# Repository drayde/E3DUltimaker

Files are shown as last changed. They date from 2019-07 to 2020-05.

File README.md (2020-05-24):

# Firmware for Ultimaker 2 with E3D v6 Hotend and Titan Extruder

This firmware is for a Ultimaker 2 with the E3D Upgrade Kit installed, which includes a E3D v6 hotend and a Titan extruder.

The firmware is a fork of the original Ultimaker firmware:
https://github.com/Ultimaker/Ultimaker2Marlin

The original README ist included as README_orig in this repro.

Changes have been made to the source code by E3D to work with the changed setup.
The orginal E3D fork is no longer online, but should match the *e3d-latest* branch in this repro.

## Links

Old wiki page on e3d-online.com: https://wiki.e3d-online.com/E3D-v6_on_Ultimaker_2
([local copy as pdf](https://github.com/drayde/E3DUltimaker/blob/drayde/E3D-v6%20on%20Ultimaker%202%20-%20E3D-Online.pdf))

Conversion video guide by Thomas Sanladerer: https://youtu.be/aLLci32tHA4

3D printed parts on thingiverse: https://www.thingiverse.com/thing:1934309

## Firmware changes by E3D

Firmware changes as documented on https://wiki.e3d-online.com/E3D-v6_on_Ultimaker_2

Changes in the "configuration.h" file:

    // increase the maximum temperature for the E3D V6 HotEnd
    #define HEATER_0_MAXTEMP 400

    // PID values for Ultimaker2 with E3D HotEnd
    #define  DEFAULT_Kp 36.59
    #define  DEFAULT_Ki 3.65
    #define  DEFAULT_Kd 91.72

    // travel extents have reduced slightly for E3D HotEnd
    #define X_MAX_POS 215 // For E3D HotEnd
    #define Y_MAX_POS 210 // For E3D HotEnd
    #define INVERT_E0_DIR true   // for direct drive extruder v9 set to true, for geared extruder set to false

    // default steps per unit for Ultimaker2 and E3D Extruder
    #define DEFAULT_AXIS_STEPS_PER_UNIT   {80.0,80.0,200,837}   // 837 to be changed to 418.5 for if a 200 steps/mm motor is used
    #define DEFAULT_MAX_FEEDRATE          {300, 300, 40, 20}    // (mm/sec)
    #define DEFAULT_MAX_ACCELERATION      {9000,9000,100,3000}  // X, Y, Z, E maximum start speed for accelerated moves. 
                                                                // E default values are good for skeinforge 40+, for older 
                                                                // versions raise them a lot.

The Bowden retraction settings should be changed if the filament change function is to work properly after the upgrade. These settings are found in the "UltiLCD2_menu_material.h" file. Here are the variables that need to be changed and their new value:

    #define FILAMENT_REVERSAL_LENGTH      (FILAMANT_BOWDEN_LENGTH + 150)
    #define FILAMENT_REVERSAL_SPEED       75
    #define FILAMENT_INSERT_FAST_SPEED    75   // Speed during the forward length

**Note:** These changes were done on an old version of the Ultimaker 2 firmware (from 29th January 2016).

The later Ultimaker 2 firmware (after v14.09) has a temperature safety feature built in, which has been notoriously sensitive. It seems like it is overly sensitive and an E3D HotEnd doesn't conform to its expected heat up and cool down cycles. The result is a common "ERROR - STOPPED Heater error" on the display panel and a failed print. The part cooling fans can often trigger this error as the air blown to cool the print can also end up cooling the heater block due to certain print geometry. Although the silicone sock provided in the kit should reduce this, it is still a recurring issue.

If you repeatedly encounter this issue, check the position of your part cooling fan ducts. They should be as low as possible without touching the bed when the nozzle does. Also, adding a siliconw sock can greatly reduce this error. Otherwise, the following lines in the "configuration.h" file control the parameters of this "safety feature".

    #define MAX_HEATING_TEMPERATURE_INCREASE 0.1 //[E3D] original value 10
    #define MAX_HEATING_CHECK_MILLIS (90000) //[E3D] original value(30 * 1000)

If you want to disable this feature like it was back in v14.09 then you can comment out the following lines in the "temperature.cpp" file at your own risk:

    // Commented out for UM2 because too sensitive for E3D HotEnd           
    //            disable_heater();
    //            Stop(STOP_REASON_HEATER_ERROR);

## My firmware changes 

none yet :-)

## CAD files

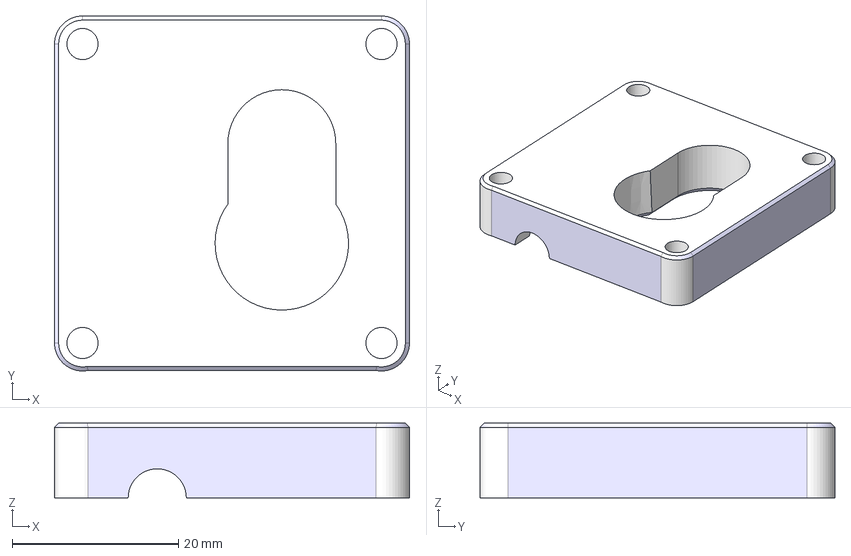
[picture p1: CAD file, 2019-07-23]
Hardware Upgrades/E3D files from thingiverse/files/P-MOUNTING-ULTIM-LAYER_2.step
42.8 x 42.7 x 9.00 mm

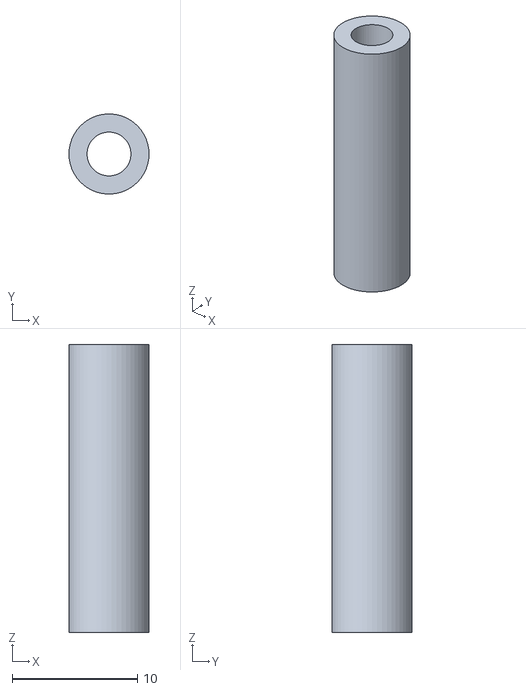
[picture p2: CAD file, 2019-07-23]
Hardware Upgrades/fan_spacer.stl
6.40 x 6.39 x 23.0

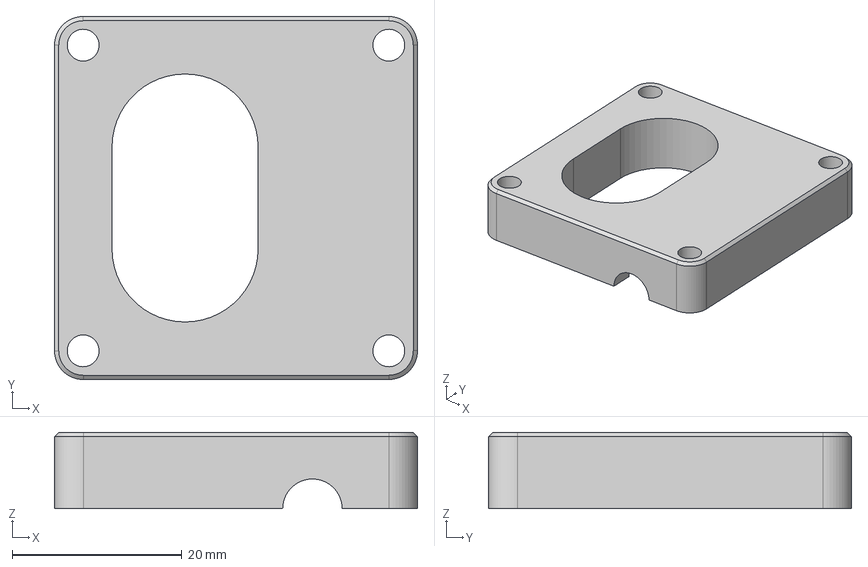
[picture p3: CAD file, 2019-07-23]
Hardware Upgrades/E3D files from thingiverse/files/P-MOUNTING-ULTIM-LAYER_4.step
42.7 x 42.7 x 9.00 mm

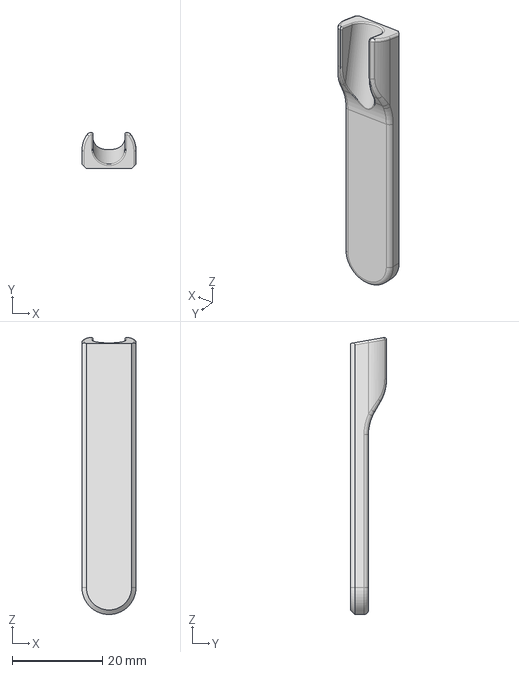
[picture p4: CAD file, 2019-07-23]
Hardware Upgrades/E3D files from thingiverse/files/P-MOUNTING-ULTIM-BOW-TOOL_II.stp
12.0 x 8.00 x 61.3 mm

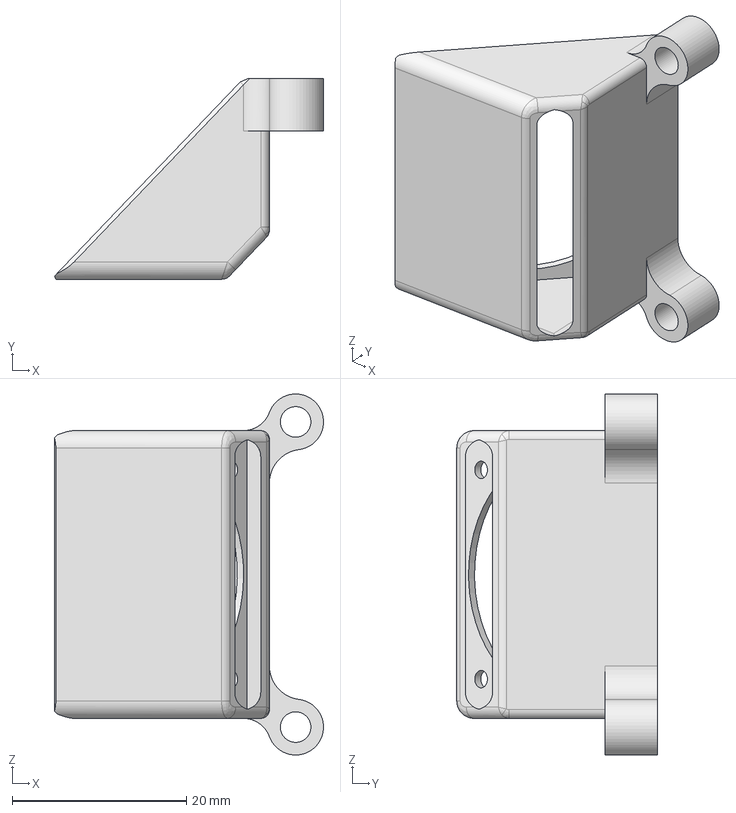
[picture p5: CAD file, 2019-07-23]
Hardware Upgrades/E3D files from thingiverse/files/P-MOUNTING-ULTIM-FAN-DUCT.stp
30.9 x 23.0 x 41.4 mm

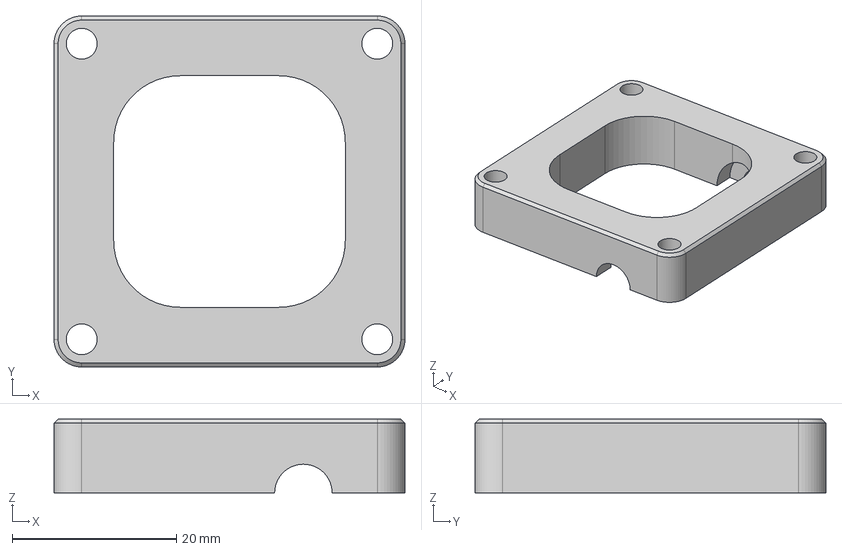
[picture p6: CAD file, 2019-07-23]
Hardware Upgrades/E3D files from thingiverse/files/P-MOUNTING-ULTIM-LAYER_3.step
42.7 x 42.7 x 9.00 mm

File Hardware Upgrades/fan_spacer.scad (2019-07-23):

// height in mm
height = 23;

// inner diameter in mm
inner_diameter = 1.75*2;

// outer diameter in mm
outer_diameter = 3.2*2;

// inner chamfer at bottom in mm (to avoid 'elephant foot' when 3d printing)
chamfer_inner = 0.4;

// inner chamfer at bottom in mm (to avoid 'elephant foot' when 3d printing)
chamfer_outer = 0.0;

/* [Hidden] */

inner_radius = inner_diameter/2;
outer_radius = outer_diameter/2;
eps = 0.001;

$fn = 50;

difference() 
{
	cylinder(h=height, r=outer_radius);
	translate([0,0,-eps]) cylinder(h=height+1, r=inner_radius);

	translate([0,0,-eps]) cylinder(h=chamfer_inner, r1=inner_radius+chamfer_inner, r2=inner_radius);
    
    translate([0,0,-eps]) difference()
    {
        cylinder(h=chamfer_outer, r=outer_radius);
        translate([0,0,-eps]) cylinder(h=chamfer_outer, r1=outer_radius-chamfer_outer, r2=outer_radius+eps);
    }
}

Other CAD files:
Hardware Upgrades/E3D files from thingiverse/files/P-MOUNTING-ULTIM-LAYER_1.step
Hardware Upgrades/E3D files from thingiverse/files/P-MOUNTING-ULTIM-BOW-TOOL.stl
Hardware Upgrades/E3D files from thingiverse/files/P-MOUNTING-ULTIM-FAN-DUCT.stl
Hardware Upgrades/E3D files from thingiverse/files/P-MOUNTING-ULTIM-LAYER_1.stl
Hardware Upgrades/E3D files from thingiverse/files/P-MOUNTING-ULTIM-LAYER_2.stl
Hardware Upgrades/E3D files from thingiverse/files/P-MOUNTING-ULTIM-LAYER_3.stl
Hardware Upgrades/E3D files from thingiverse/files/P-MOUNTING-ULTIM-LAYER_4.stl

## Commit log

2019-07-23 import E3D 3d printed files
    [P-MOUNTING-ULTIM-BOW-TOOL.stl, P-MOUNTING-ULTIM-BOW-TOOL_II.stp, P-MOUNTING-ULTIM-FAN-DUCT.stl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]
2019-07-23 added fan spacer STL
    [fan_spacer.scad, fan_spacer.stl]
